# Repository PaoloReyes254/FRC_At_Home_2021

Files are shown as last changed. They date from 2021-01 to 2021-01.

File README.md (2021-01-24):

# **WINT 3794 FRC AT HOME 0$ ROBOT IDEA**

The initial idea is to create a competitive robot that can accomplish all FIRST at home challenges with a 0 dollars budget.

The chasis will be the same as WinT 3794 FRC 2020 robot with the only change of pneumatic wheels to HiGrip 6 inches wheels.

The chasis consist of 6 NEO motors (3 per side) chain driven with 2 REV throughBore encoders at the lasts wheels to perform autonomous tasks using differential equations.

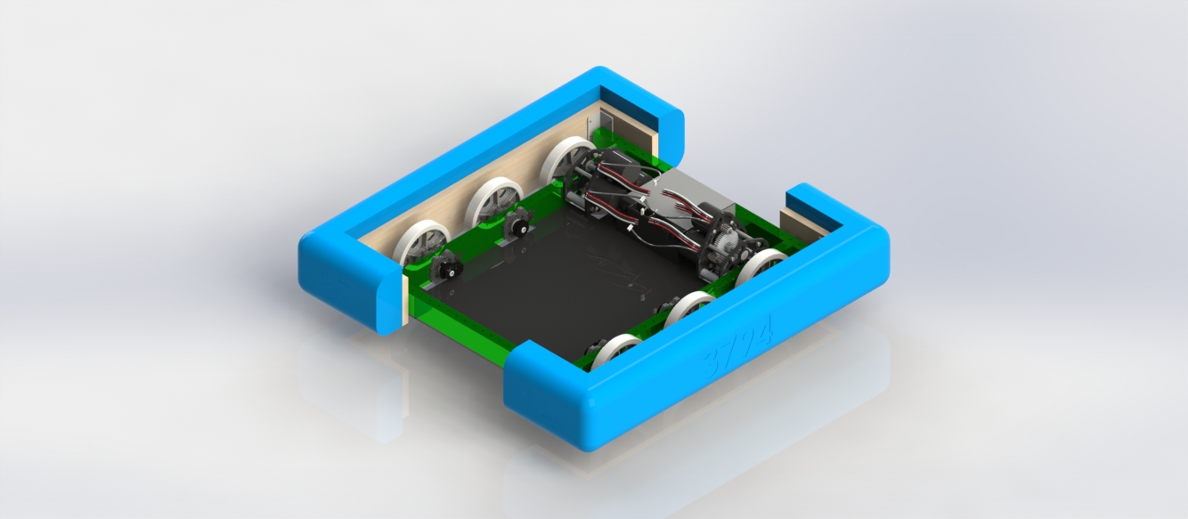
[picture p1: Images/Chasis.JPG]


Now let's approach how to improve this robot to accomplish all First At Home tasks.

---
# **Galactic Search Challenge**

*"In the Galactic Search challenge, teams emulate the Autonomous Period of INFINITE RECHARGE
gameplay by locating and collecting POWER CELLS as fast as they can on one of two (2) pairs of paths."*

**IMPORTANT RULES**

*"GSC2. Teams must randomly determine (e.g. coin, die, phone app, etc.) if they run the red or blue paths.
Teams make a single random determination and then run the same color on both paths.
The intent is that teams do not signal directly to the ROBOT which option has been
chosen. Placement of the ROBOT is not considered signaling."*

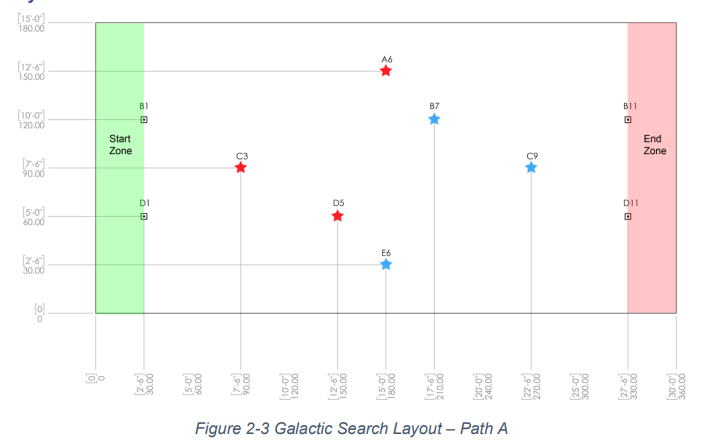
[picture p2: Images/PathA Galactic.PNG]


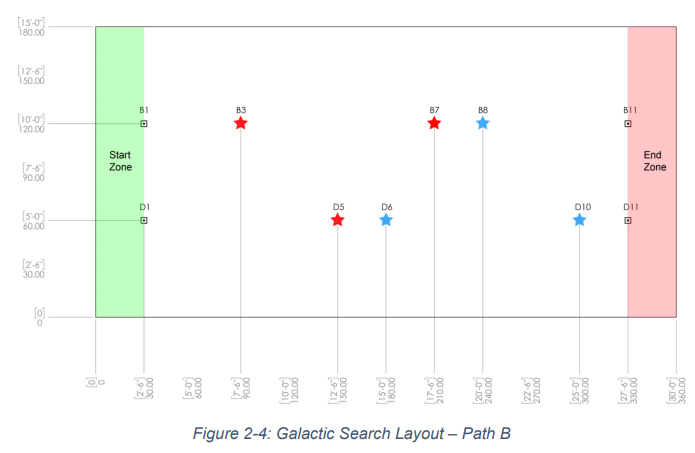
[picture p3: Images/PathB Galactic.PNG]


# What do we need to accomplish this?

In this challenge we need a fast intake to collect the three balls, another thing to have in consideration is robot's center of mass to be able to run at 100% speed without risk, we also need a certain type of feedback to know the position of the robot so it can move to all three positions of the balls consistently and some kind of vision to let the robot know if is going to do red stars or blue stars.

I think the best way to approach this is by keeping a low profile robot, use the already existing REV encoders as position feedback, a passive intake activated with servos due to lack of motors and pneumatic and a webcam with OpenCv to determine whether we are going to do red or blue stars.

---
# Intake Design
To design the intake I consider two main things.

1. The intake needs two rollers to overcome the bumper and move the ball with enough X direction force inside the robot.
1. Needs to be as simple as possible.

For that reason I got this intake design:

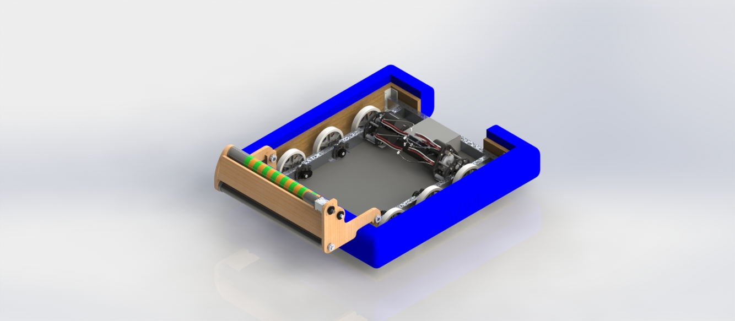
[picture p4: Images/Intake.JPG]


This intake is made out of MDF, it has a PVC roller and 16 2.25 inches compliant wheels on top, it is driven through chain and a 775 motor with a 10:1 gearbox.
With this simple robot we should be able to complete challenge #1 and the only thing that is missing is how to deploy the intake without any motor or pneumatic system.

To solve the **how to deploy the intake** problem I used 2 servos to lock the intake and then those servos will be moved to let the intake fall by gravity and elastic rubber bands.
You will understand better with the following images:

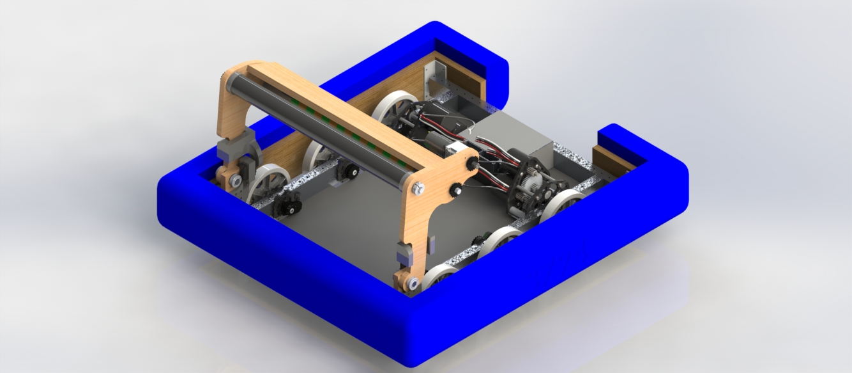
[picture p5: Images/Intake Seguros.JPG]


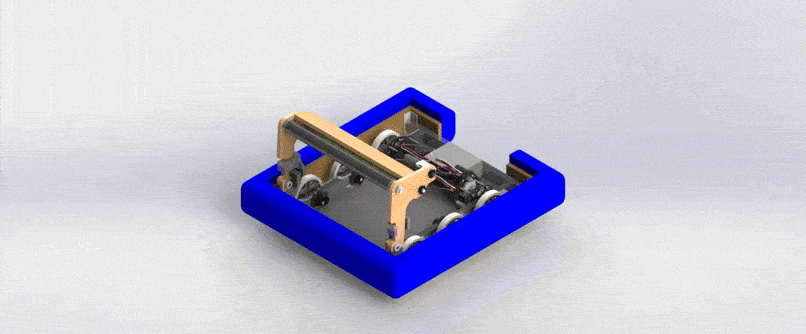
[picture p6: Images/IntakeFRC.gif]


Finally I will add a camera on top of the intake to determine which path we will go to play.

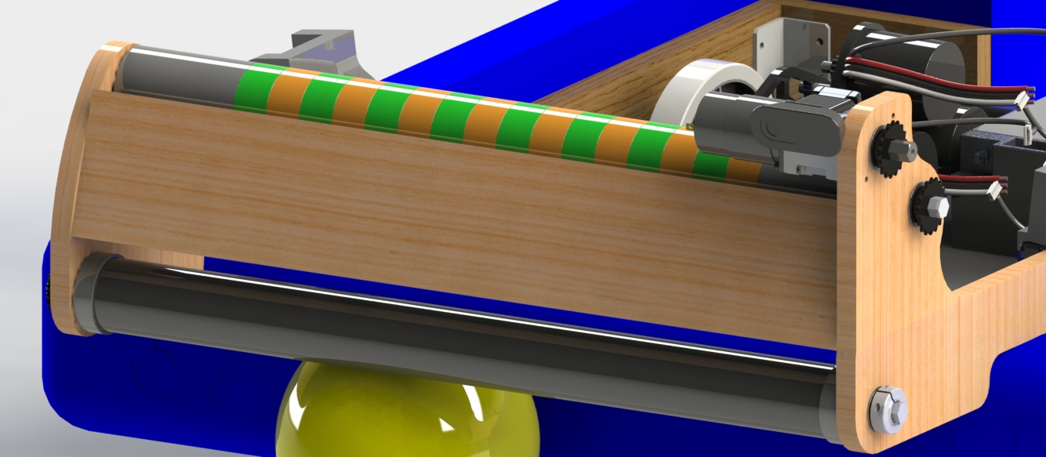
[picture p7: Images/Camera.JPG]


---
# **AutoNav Challenge**

*"In the AutoNav Challenge teams program their ROBOTS to autonomously drive predetermined routes
through three (3) different paths as fast as possible."*

For this challenge we only need a fast chassis with some encoder feedback, so we must be fine with our actual robot.

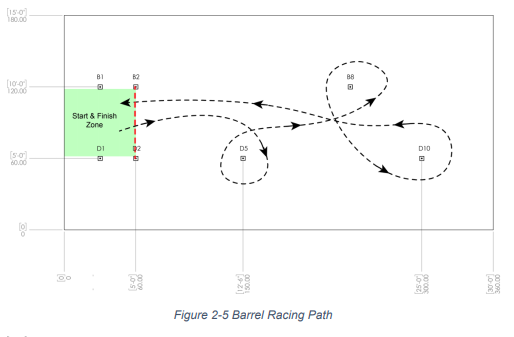
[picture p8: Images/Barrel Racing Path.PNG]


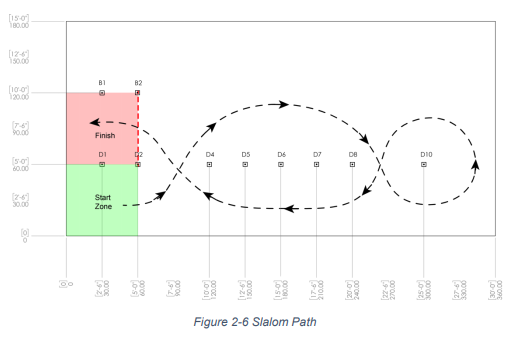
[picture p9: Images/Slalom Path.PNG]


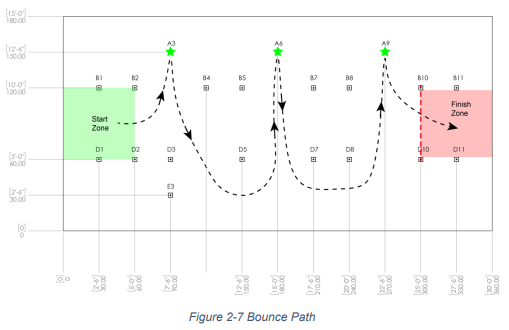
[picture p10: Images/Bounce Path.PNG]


---
# **Hyperdrive Challenge**

*In the Hyperdrive Challenge teams drive their ROBOTS remotely, without the assistance of preprogrammed navigation, through four (4) different paths as fast as possible. The first three (3) paths are
the same as those described in AutoNav Challenge, the fourth path is the Lightspeed Circuit path.*

To accomplish this challenge we only need a good driver and the robot should work as it is designed now.







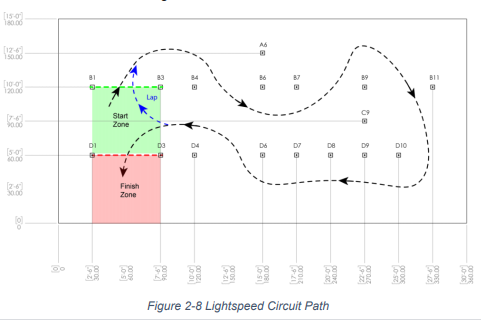
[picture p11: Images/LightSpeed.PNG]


---

# **Interstellar Accuracy Challenge**

*In the Interstellar Accuracy Challenge teams emulate the shooting challenges of INFINITE RECHARGE
gameplay by scoring POWER CELLS into a representation of the BOTTOM PORT, OUTER PORT, AND
INNER PORT from four (4) zones. Teams will attempt to score as many points as possible in five (5)
minutes.*

**Important Rules**

1. Teams may not attempt more than fifteen (15) POWER CELL shots.
1. Teams must attempt at least three (3) POWER CELLS per zone. The remaining three (3)
POWER CELLS may be shot from any of the four (4) zones.
1. The ROBOT may not be preloaded with more than three (3) POWER CELLS such that they are
fully and solely supported by the ROBOT.
1. No more than two (2) people may feed POWER CELLS to the ROBOT.
1. The ROBOT must be completely within the Reintroduction Zone in order to acquire POWER
CELLS from humans.

**Scoring**

- BOTTOM PORT = 1 Point
- OUTER PORT = 2 Points
- INNER PORT = 3 Points

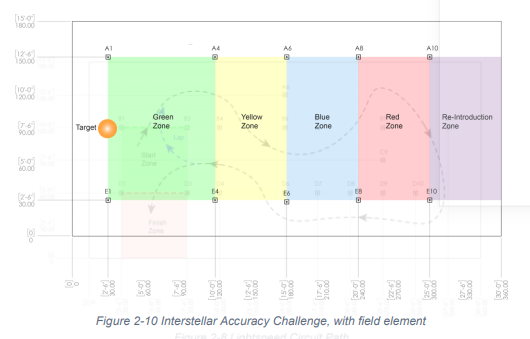
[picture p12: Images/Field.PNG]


---
# What do we need to accomplish this?

A fast indexer, a fast way for human players to introduce balls, a very accurate shooter and an adjustable angle to be able to shoot from all different 4 spots.

---
# Indexer Design
**Requirements:**

1. It must use only 1 motor.
1. It should be able to keep 3 balls.
1. It should be open for human players to introduce balls as quick as possible. 

The first part of the indexer consist of a conveyor belt in the floor to transport balls.

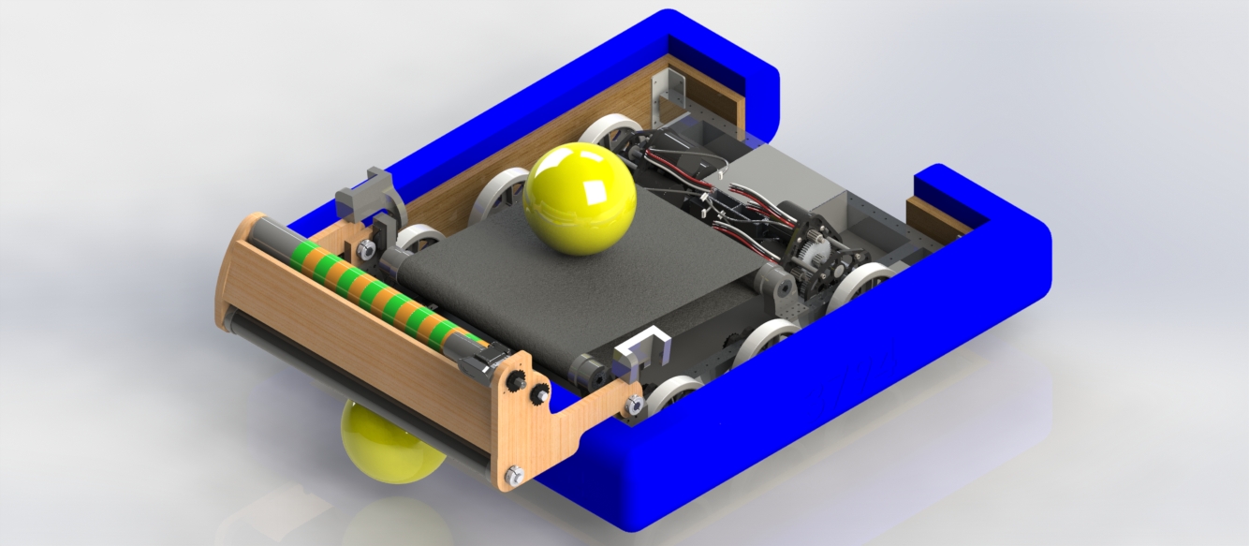
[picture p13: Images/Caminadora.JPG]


The conveyor belt will be built with **Home Depot** Non-slip tape.



Then the second part of the indexer consist of side conveyors to center the ball at the end.

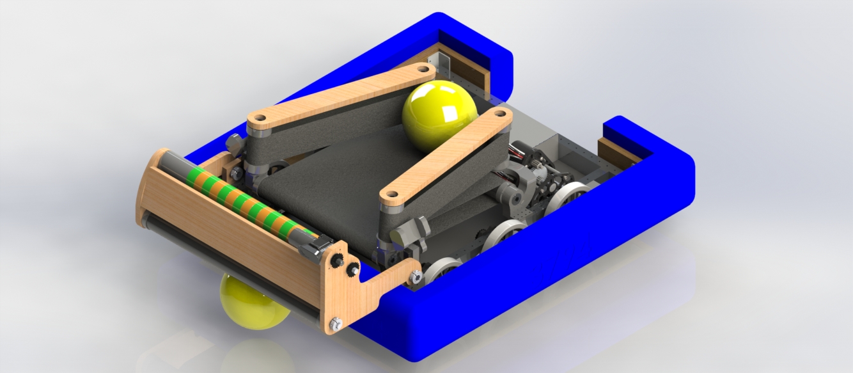
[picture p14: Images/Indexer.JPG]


Finally I will add the motor and the needed gears to make it run.

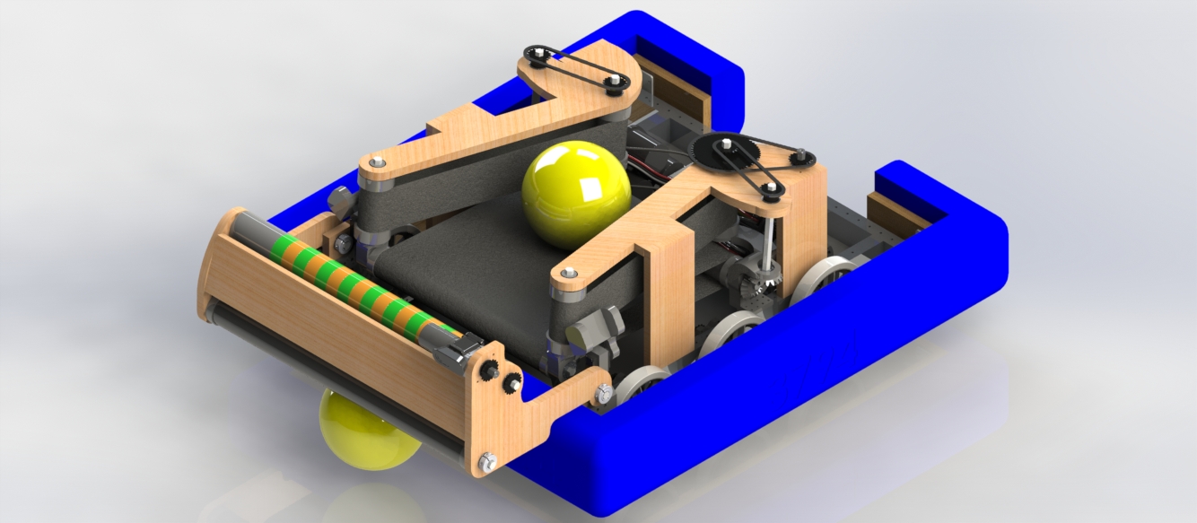
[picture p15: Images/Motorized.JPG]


---

# Shooter Design
**Requirements:**

1. It must use 4 motors.
1. It should be able to shoot in the opposite direction of the intake.
1. It should have an adjustable angle. 

The shooter consist of a 4 inches compliant wheel roller at the bottom to transport balls from indexer toward flywheel, the flywheel has 4 775pro 1:1 geared motors with an external 2:1 reduction that we can change if we need, then we have 4 inches colson wheels to shoot the balls at a theoretical speed of 9000rpm and finally an adjustable shooting angle driven by 2 servos.

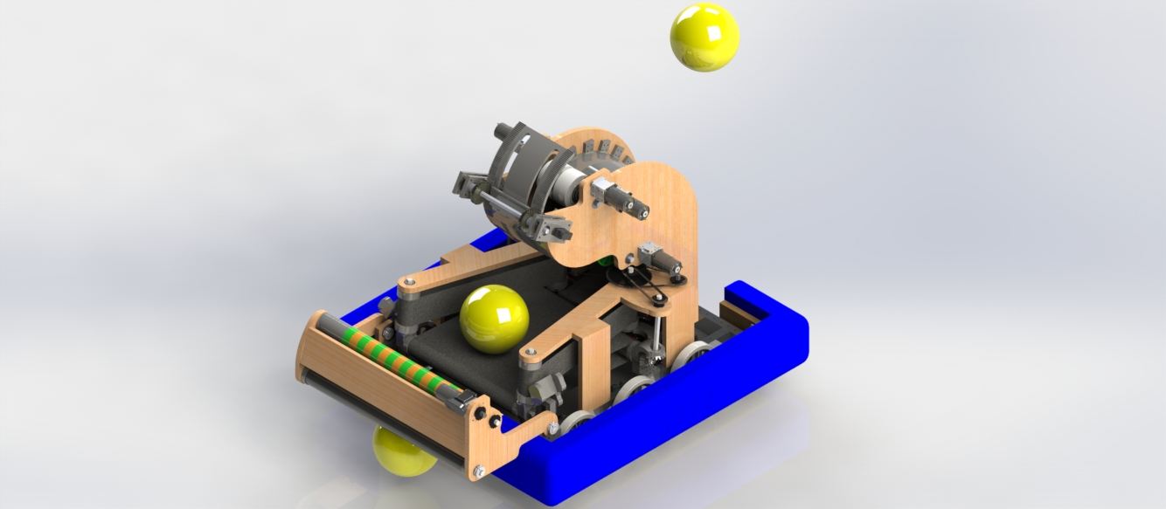
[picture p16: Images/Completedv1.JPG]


Finally I added the limelight and a logo of the team.

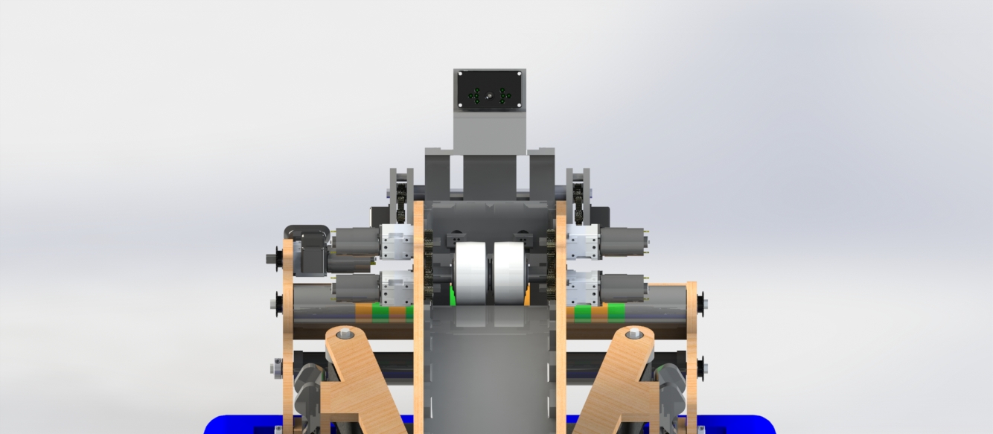
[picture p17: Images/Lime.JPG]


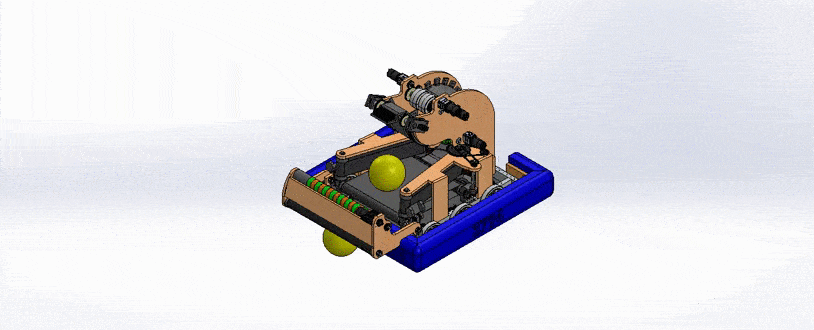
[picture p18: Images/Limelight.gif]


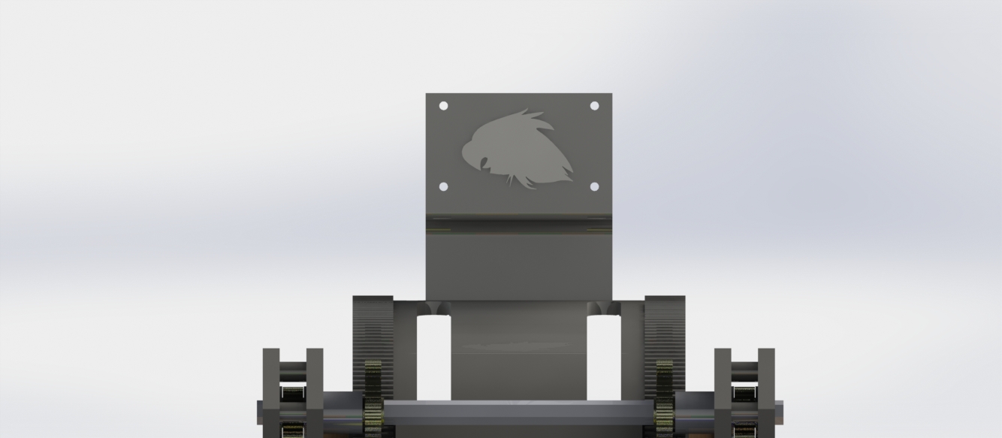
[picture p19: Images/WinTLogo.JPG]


---
# **POWER PORT Challenge**

*In the POWER PORT Challenge teams emulate the teleoperated portion of INFINITE RECHARGE
gameplay by collecting POWER CELLS and scoring them into a representation of the POWER PORT.
Teams attempt to score as many points as possible in the POWER PORT in one minute.*

**Important Rules**

1. Teams may not use more than three (3) POWER CELLS.
1. The ROBOT must start completely within the challenge space.
1. The ROBOT may be preloaded with up to three (3) POWER CELLS
1. The ROBOT may only attempt a shot if its BUMPERS are fully contained within the Scoring Zone
which extends 17 ft. 6 in (~533 cm) from the face of the POWER PORT representation.
1. No more than two (2) people may feed POWER CELLS to the ROBOT.
1. POWER CELLS may be introduced directly to the ROBOT or onto the floor.
POWER CELLS which land in the challenge space may be fielded directly by the ROBOT
anywhere in the challenge space; they do not need to be reintroduced by a human or into
the Reintroduction Zone.
Use of a LOADING BAY (or LOADING BAY mockup) is recommended to minimize risk of
human injury by a POWER CELL receiving ROBOT.
The intent of this allowance is to avoid forcing humans to field POWER CELLS in close
proximity to the ROBOT. Teams should not use this allowance to attempt to create a
"loop" with minimal ROBOT movement.

**Scoring**

- BOTTOM PORT = 1 Point
- OUTER PORT = 2 Points
- INNER PORT = 3 Points

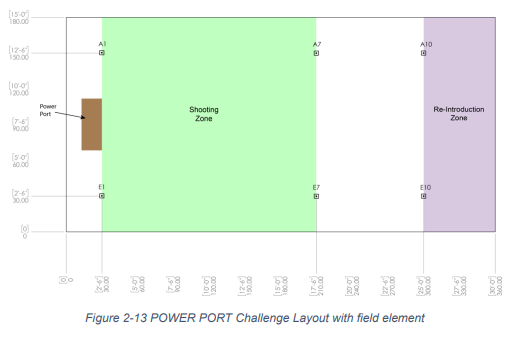
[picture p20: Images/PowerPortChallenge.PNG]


With the actual robot we should be able to accomplish this challenge, so there are no more modifications.

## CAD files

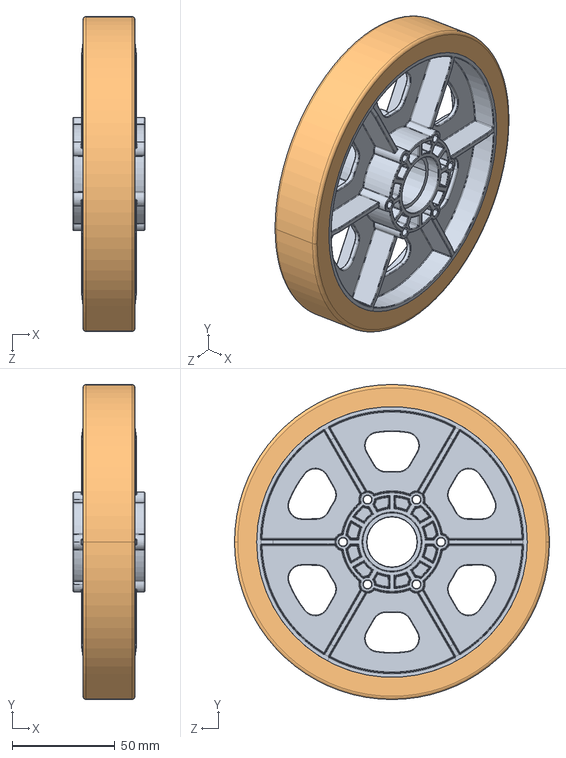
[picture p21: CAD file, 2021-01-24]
Robot 2020/Wheel.SLDASM
34.9 x 153.2 x 153.2 mm
6 wheel Rev 4.STEP
SmoothGrip Tread.STEP

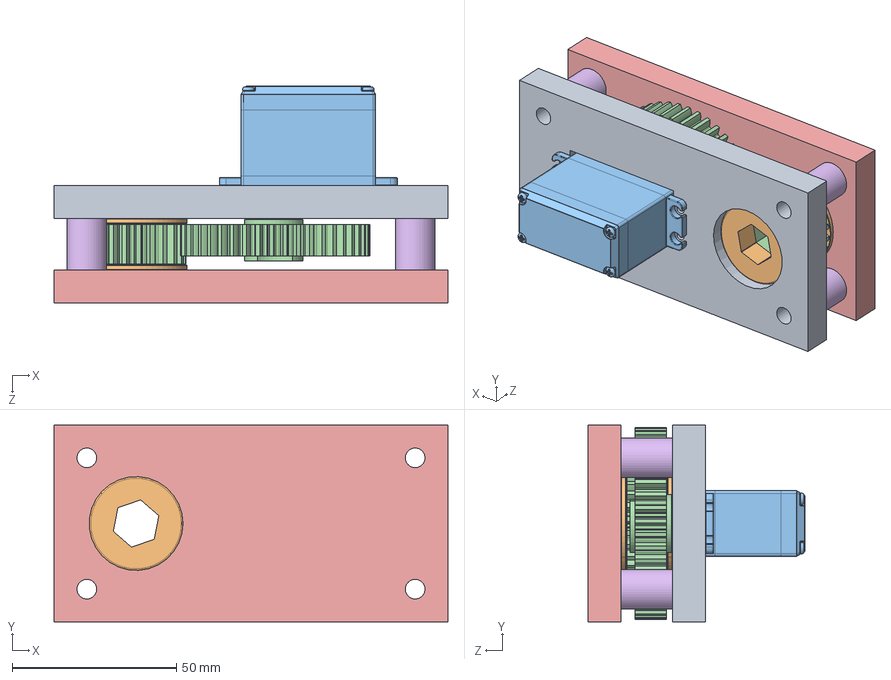
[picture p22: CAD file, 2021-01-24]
Parts/ServoGearbox.SLDPRT.SLDASM
120.0 x 60.0 x 66.0 mm
ServoGearbox
Hex bearing x 2
MG995-MG996R Servo.stp
WCP Aluminum Hex Bore Gears x 2
GearboxPlate
Espaciador Gearbox x 4

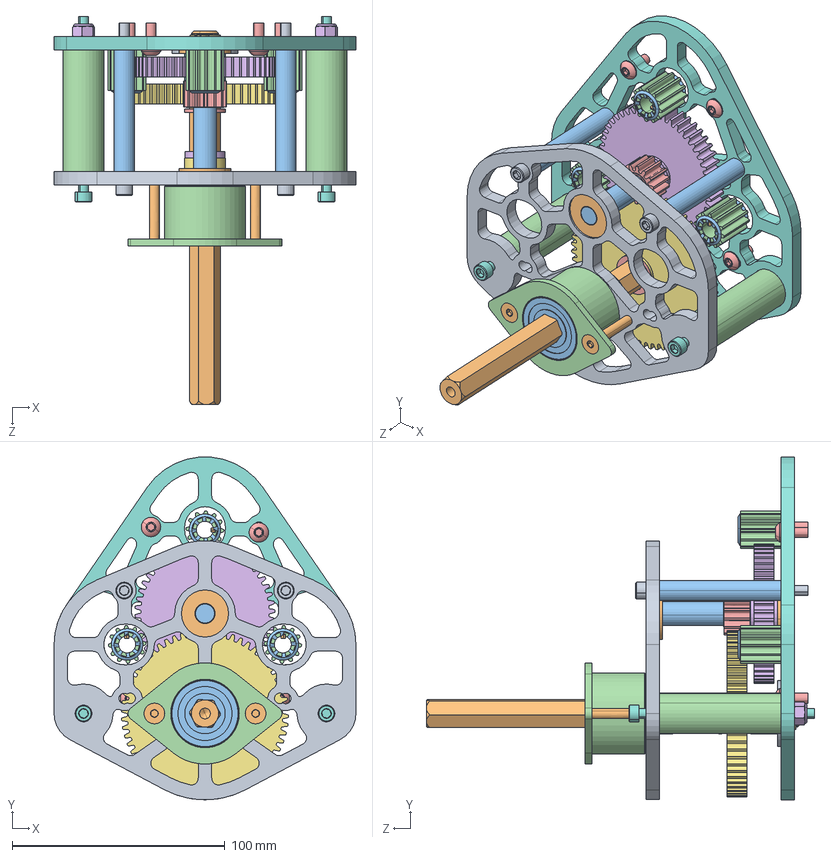
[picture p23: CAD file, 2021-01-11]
Parts/Gearbox chassis.SLDASM
142.1 x 161.3 x 182.6 mm
217-2731.STEP
217-2733.STEP x 2
217-2734.STEP
217-3099-001_12t.STEP x 3
217-3100-001_14t.STEP
217-2711-002 Rev1_50t.STEP
217-2714-002 Rev1_60t.STEP
217-3421-001 Rev1.STEP
217-3421-002 Rev1.STEP
217-3421-004 Rev1.STEP
217-3422-001 Rev1.STEP
217-3422-004 Rev2.STEP
217-3421-009 Rev1.STEP x 4
217-3421-010 Rev1.STEP x 2
217-3421-011 Rev2_97633A200.STEP
217-3422-005 Rev1.STEP x 2
217-3422-006 Rev1.STEP x 2
217-3422-007 Rev1.STEP x 2
217-3422-002 Rev1.STEP x 2
217-3422-003 Rev1.STEP x 2
217-3257-001 Rev1.STEP x 2
217-2758-001 Rev1.STEP
217-3259-001 Rev1.STEP
217-3261-001 Rev1.STEP
217-3263-001 Rev1.STEP
217-2761-001 rev1.STEP x 3
217-2614-002_98430A132.STEP x 6

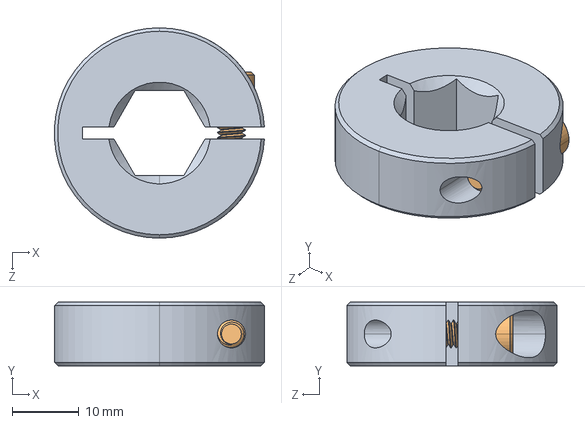
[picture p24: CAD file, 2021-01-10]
Parts/Collar Clamp, 0.5'' Hex Bore, Aluminum REV2.SLDASM
31.4 x 9.53 x 31.5 mm
am-1238 Clamp Only.STEP
am-1238 Screw Only_91251A194.STEP

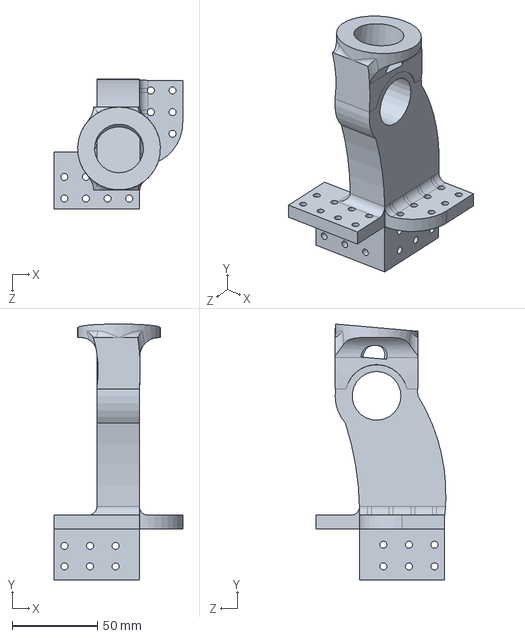
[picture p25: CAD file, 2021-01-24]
Parts/Camindora2.SLDPRT
75.4 x 150.1 x 76.0 mm

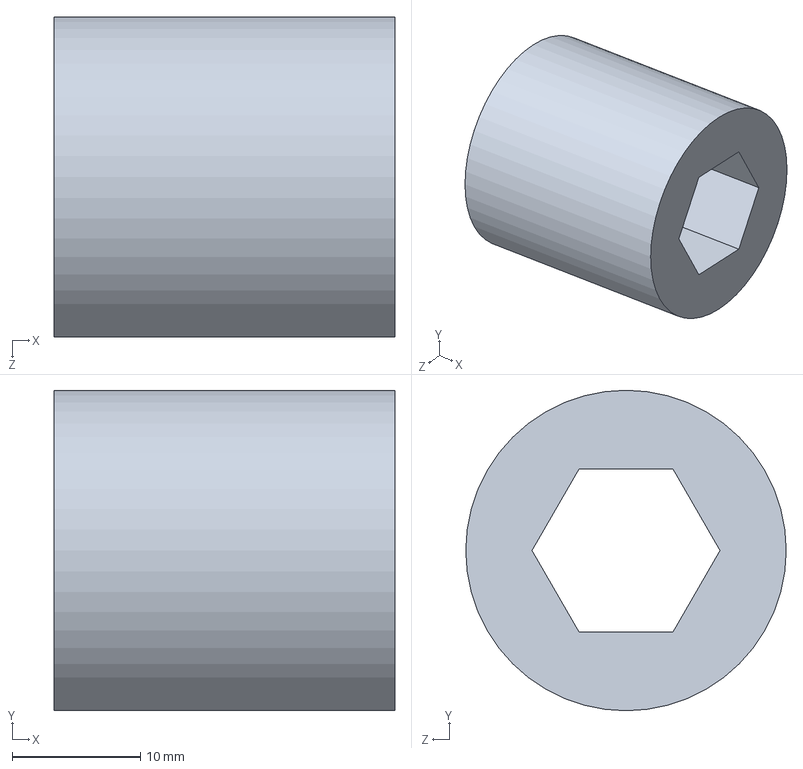
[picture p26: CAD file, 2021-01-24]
Parts/EspaciadorAngle.SLDPRT
26.6 x 25.0 x 25.0 mm

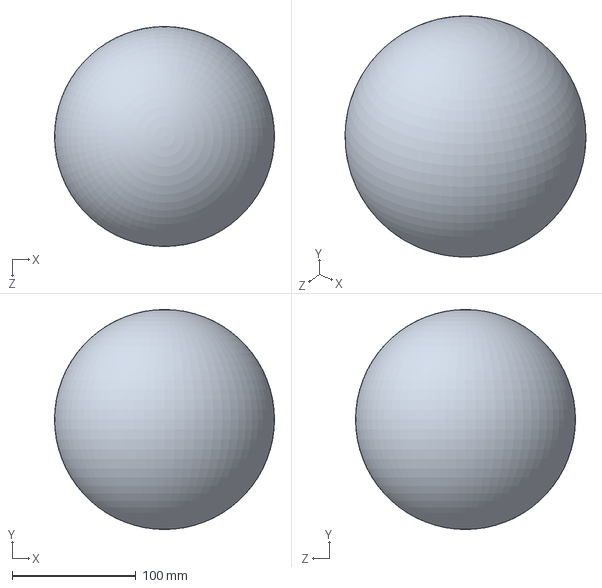
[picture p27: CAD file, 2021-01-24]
Robot 2020/power cell.SLDPRT
177.8 x 177.8 x 177.8 mm

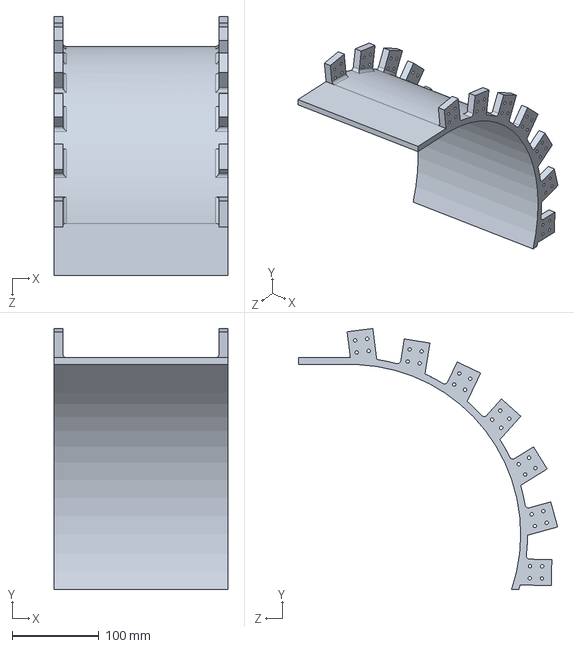
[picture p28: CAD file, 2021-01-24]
Parts/ToboganP1.SLDPRT
200.2 x 301.1 x 299.2 mm

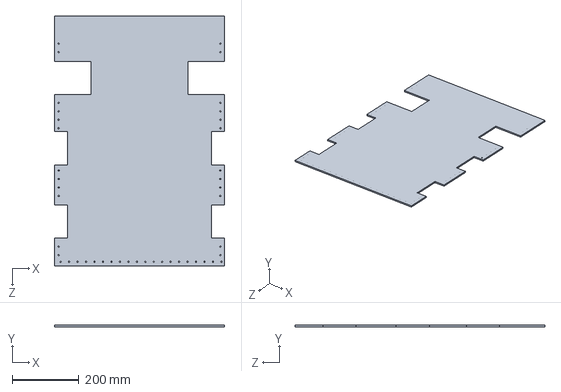
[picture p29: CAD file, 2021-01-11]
Robot 2020/Base chasis robot 2021.SLDPRT
511.0 x 5.00 x 750.8 mm

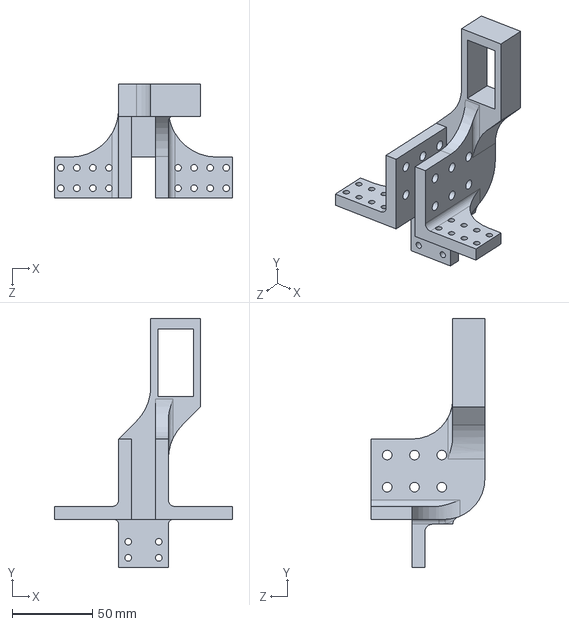
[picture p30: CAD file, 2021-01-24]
Parts/SoporteServoIntake2.SLDPRT
111.0 x 155.0 x 70.8 mm

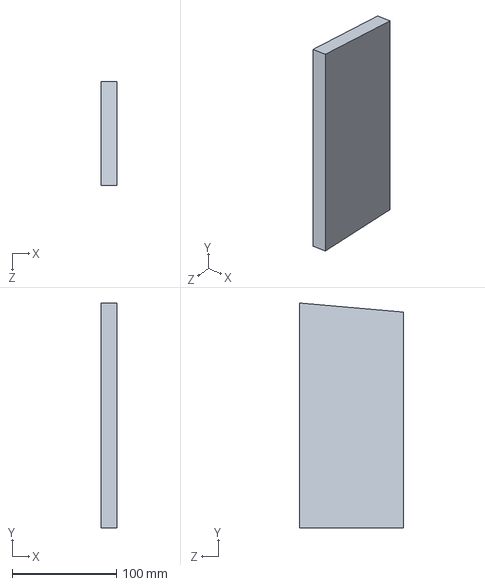
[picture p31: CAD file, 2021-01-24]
Parts/Soporte Indexer2.SLDPRT
15.0 x 216.2 x 100.0 mm

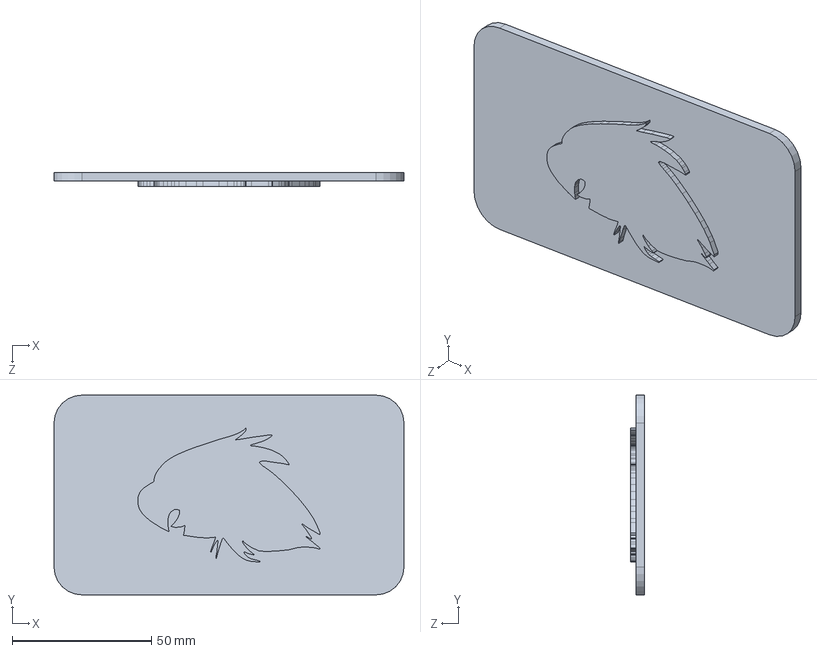
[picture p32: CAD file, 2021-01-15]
Parts/Tapa trasera.SLDPRT
125.7 x 71.7 x 5.00 mm

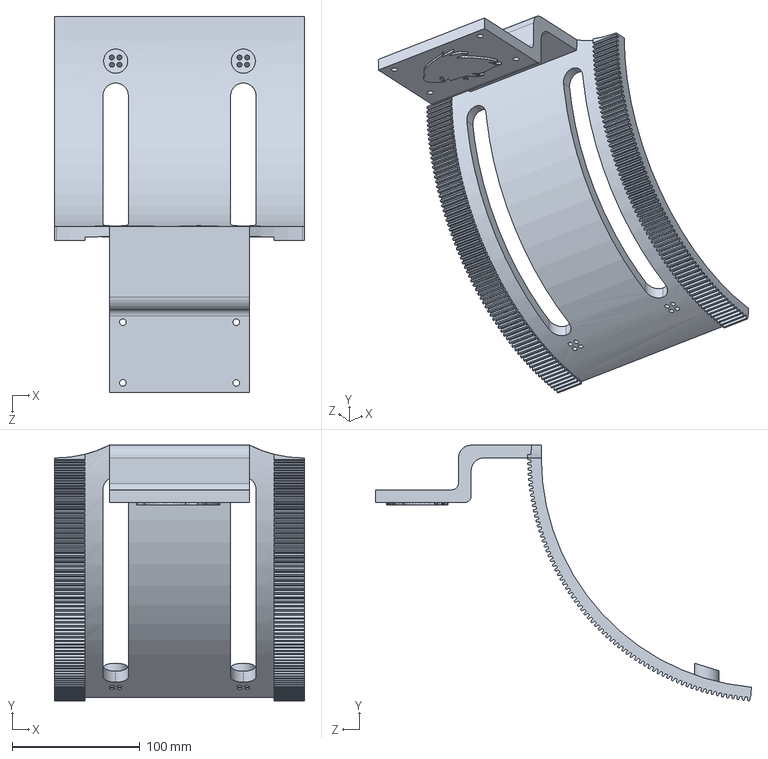
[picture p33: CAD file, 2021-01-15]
Parts/ShooterHood2.SLDPRT
196.0 x 200.5 x 294.8 mm

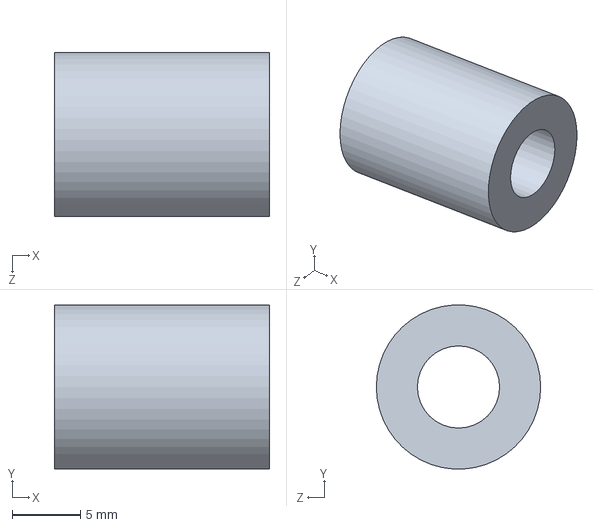
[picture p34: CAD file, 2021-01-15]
Parts/Espaciador Gearbox.SLDPRT
15.7 x 12.0 x 12.0 mm

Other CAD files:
Parts/EspaciadoShooter2.SLDPRT
Parts/Flecha shooter.SLDPRT
Parts/Seguro Shooter.SLDPRT
Parts/WCP Aluminum Hex Bore Gears.SLDPRT
Parts/3D printed Wheels.SLDPRT
Parts/Battery.SLDPRT
Parts/Bevel.SLDPRT
Parts/BevelIndexer.SLDPRT
Parts/Bumper Corner Bracket.SLDPRT
Parts/Bumper Enfrente.SLDPRT
Parts/Bumper.SLDPRT
Parts/BumperLleno.SLDPRT
Parts/CaminadoraRodillo2.1.SLDPRT
Parts/CaminadoraRodillo2.2.SLDPRT
Parts/Camindora.SLDPRT
Parts/Colson_Performa_4_x_0_875_1_2_Hex_bore_217-4049.STEP
Parts/Eje PCV.SLDPRT
Parts/Espaciador Indexer.SLDPRT
Parts/Espaciador Intake1.SLDPRT
Parts/EspaciadorGearbox.SLDPRT
Parts/EspaciadorIndexer.SLDPRT
Parts/EspaciadorShooter2.SLDPRT
Parts/External Retaining Ring.SLDPRT
Parts/Flecha Intake Gigante.SLDPRT
Parts/Flecha Intake.SLDPRT
Parts/FlechaAngle.SLDPRT
Parts/FlechaIndexer1.SLDPRT
Parts/FlechaIndexer2.SLDPRT
Parts/FlechaIndexer3.SLDPRT
Parts/FlechaIndexer4.SLDPRT
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

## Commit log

2021-01-11 Chasis Adapted
    [Base chasis robot 2020.SLDPRT, Base chasis robot 2021.SLDPRT, Battery.SLDPRT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]
2021-01-12 Intake Designed
    [3D printed Wheels.SLDPRT, Eje PCV.SLDPRT, Espaciador Intake1.SLDPRT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]
2021-01-12 Intake Deployment System
    [MG995-MG996R Servo.stp, SoporteIntake.SLDPRT, SoporteIntake2.SLDPRT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]
2021-01-12 Intake Deployment
    [3D printed Wheels.SLDPRT, Perfil chasis 651mm.SLDPRT, Perfil chasis 655 mm.SLDPRT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]
2021-01-12 Camera in Intake
    [REV-39-1598.STEP, Suelo.SLDPRT]
2021-01-12 Camera Image
2021-01-13 Indexer Image Added
    [CaminadoraRodillo2.1.SLDPRT, CaminadoraRodillo2.2.SLDPRT, Camindora.SLDPRT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]
2021-01-13 Gramatical Error
    [Wheel.SLDASM]
2021-01-14 Motorizing Indexer
    [Bevel.SLDPRT, BevelIndexer.SLDPRT, CaminadoraRodillo2.1.SLDPRT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]
2021-01-15 Almost there
    [Colson_Performa_4_x_0_875_1_2_Hex_bore_217-4049.STEP, EspaciadoShooter2.SLDPRT, Espaciador Gearbox.SLDPRT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]
2021-01-15 Final Tweaks in Shooter
    [ShooterHood2.SLDPRT, Tapa trasera.SLDPRT, Wheel.SLDASM]
2021-01-24 Final Gramatical tweak
    [Camindora2.SLDPRT, EspaciadorAngle.SLDPRT, ServoGearbox.SLDPRT.SLDASM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]
